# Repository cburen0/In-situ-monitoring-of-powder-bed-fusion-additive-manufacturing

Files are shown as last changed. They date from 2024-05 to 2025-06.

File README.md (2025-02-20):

# In situ monitoring of powder bed fusion additive manufacturing
Hardware and software designs for in situ systems for laser-based powder bed fusion additive manufacturing.

<p align="center">
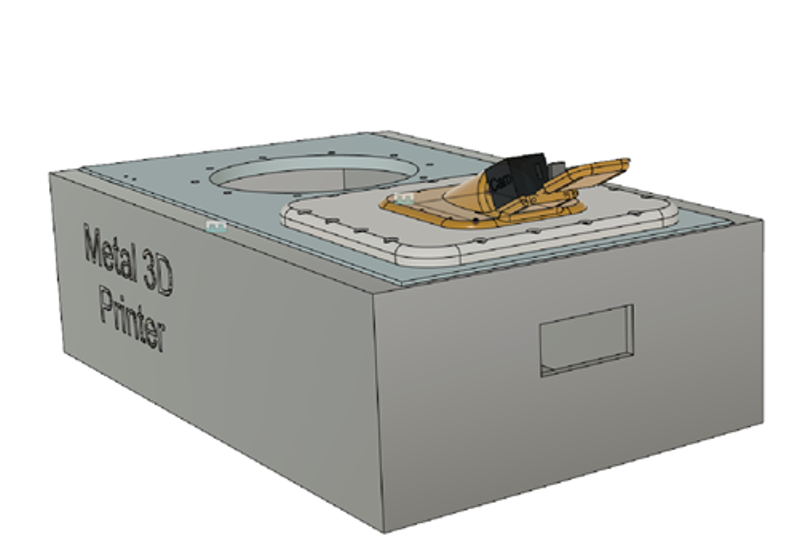
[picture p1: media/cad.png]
 <br> 
The CAD model of in situ systems for laser-based powder bed fusion additive manufacturing. 
</p>

<p align="center">
 <br> 
The Camera setup of in situ systems for laser-based powder bed fusion additive manufacturing.  
</p>

## [System Development](system_development)
The system (hardware and software) design for the project.

## [Aconity MIDI – 3D Reference Models](Aconity_MIDI–3D_Reference_Models)
Simple CAD models for the Aconity MIDI printer used for visualization purposes.

## Licensing and Citation

This work is licensed under a Creative Commons Attribution-ShareAlike 4.0 International License [cc-by-sa 4.0].



#### Bibtex

@Misc{ARTSLabSituMonitoringPowder,  
  author = {{ARTS-L}ab},  
  title  = {In situ monitoring of powder bed fusion additive manufacturing},  
  groups = {{ARTS-L}ab},  
  url    = {https://github.com/ARTS-Laboratory/In-situ-monitoring-of-Powder-bed-fusion-additive-manufacturing},  
}  

<p align="center">
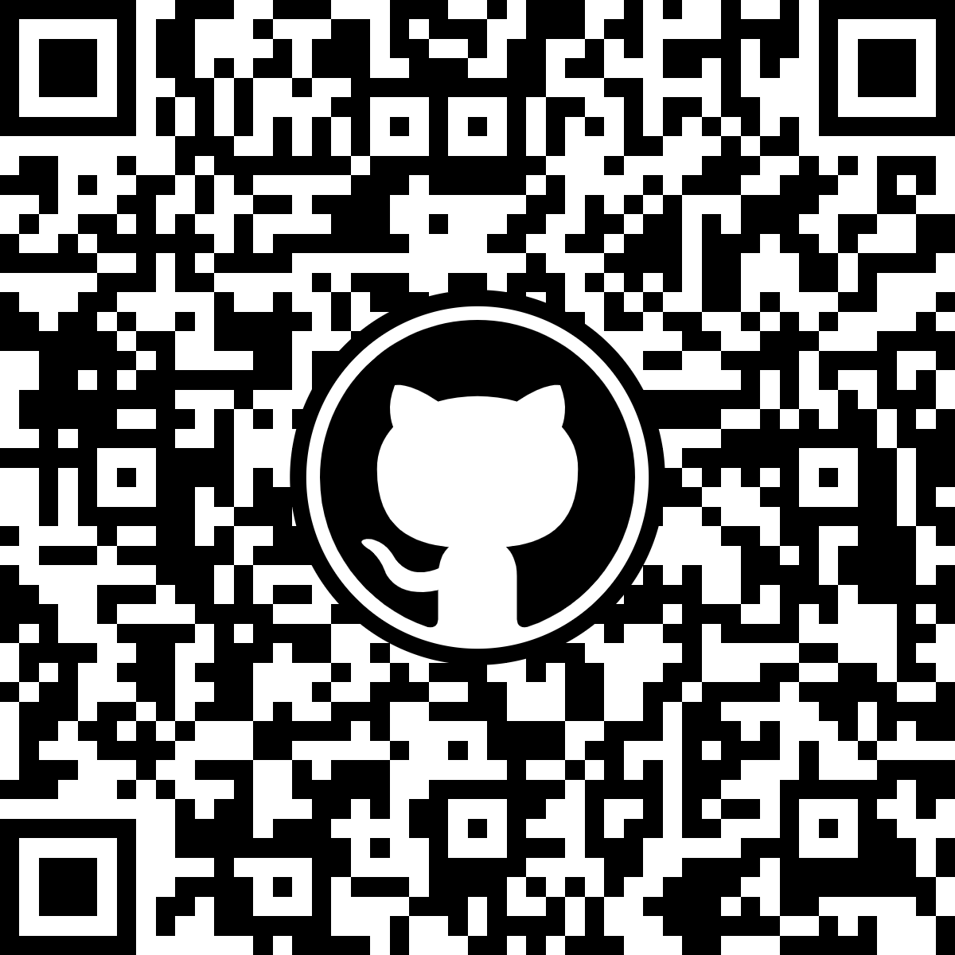
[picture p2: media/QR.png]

</p>
<p align="center">
QR code for repo.
</p>

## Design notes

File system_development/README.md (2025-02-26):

# Systems Variations  
Different system variations (i.e. product lines) are named after mythical materials. 

## Mithril
* A legendary, lightweight, and strong metal from Tolkien’s Middle-earth.
* Sensing system designed with a optical camera.

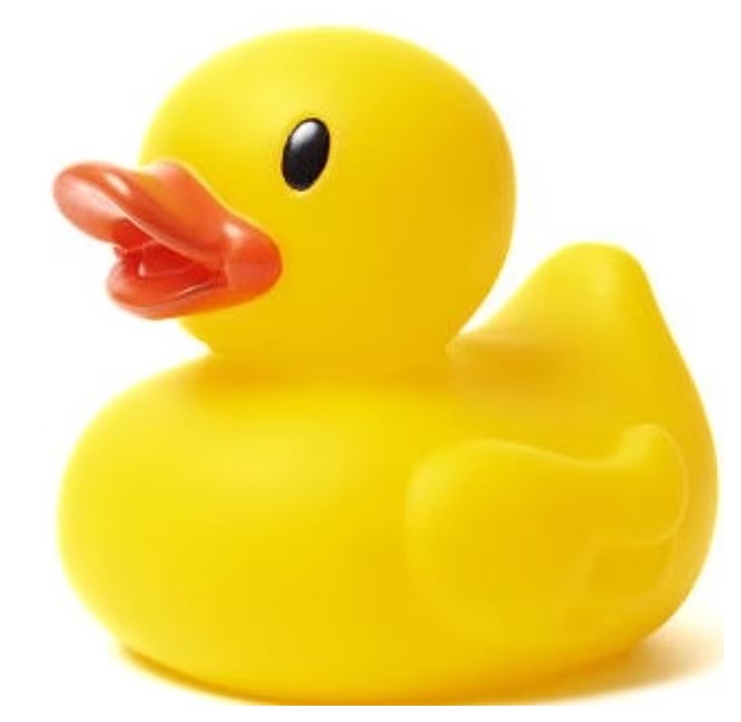
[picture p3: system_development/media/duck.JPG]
 <br> 
The CAD model of in situ systems for laser-based powder bed fusion additive manufacturing. 
</p>

## Adamant
* An ancient term for an unbreakable, diamond-like substance.
* Sensing system designed with a thermal camera.

 <br> 
The CAD model of in situ systems for laser-based powder bed fusion additive manufacturing. 
</p>

## Uru
* A mystical Asgardian metal, known for its magical properties.
* Sensing system designed with an event camera.

 <br> 
The CAD model of in situ systems for laser-based powder bed fusion additive manufacturing. 
</p>

## Orichalcum
* A lost golden-red metal from Atlantis and Greek mythology.
* Sensing system designed with a laser vibrometer.

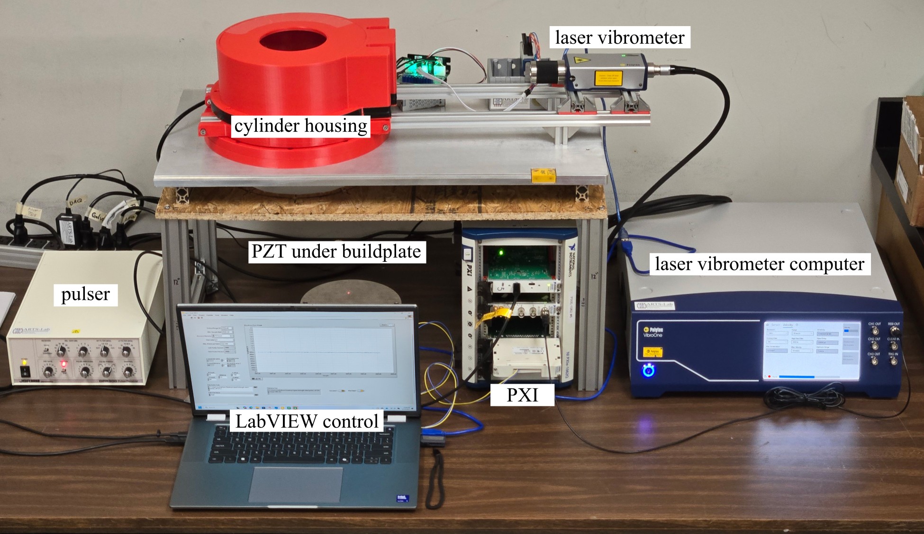
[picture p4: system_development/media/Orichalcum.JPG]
 <br> 
Experimental setup including custom cover assembly, laser vibrometer, piezoelectric transducer, and pulser. 
</p>

## Damascus
* A famed patterned steel, known for strength and sharpness.
* Sensing system designed with multiple sensing systems.

 <br> 
The CAD model of in situ systems for laser-based powder bed fusion additive manufacturing. 
</p>

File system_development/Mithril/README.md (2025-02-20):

# Mithril
Sensing system designed with an optical camera.

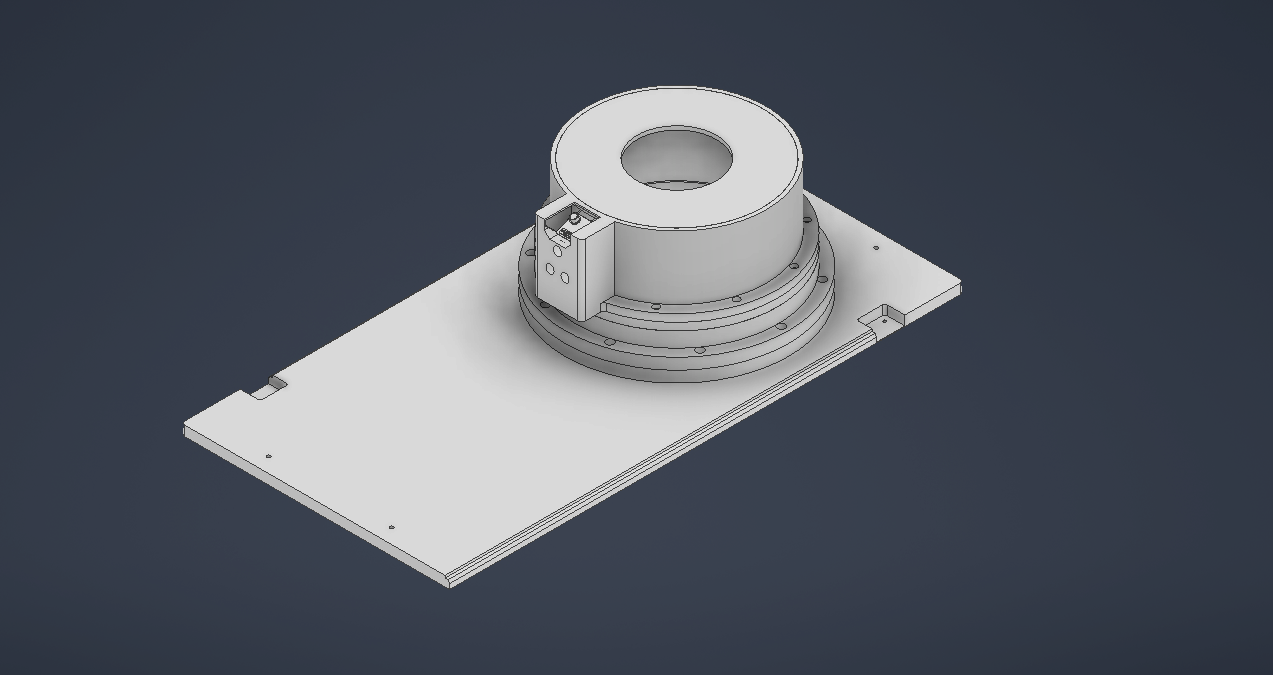
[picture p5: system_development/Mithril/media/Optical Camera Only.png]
 <br> 
The CAD model of in situ systems for laser-based powder bed fusion additive manufacturing. 
</p>

## V0.1
1. Optical camera holder for FLIR.

## V0.2

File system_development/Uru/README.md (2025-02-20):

# Uru
Sensing system designed with an event camera.
## V0.1
1. ...

## V0.2

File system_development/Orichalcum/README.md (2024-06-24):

# Orichalcum
An in situ sensing system with a laser vibrometer.

## V0.1 - Exploriotority 
Initial hardware design for in situ monitoring system.

## V0.2 - System Built as Sub-components
Initial hardware design for in situ monitoring system.

## V0.3 - First Single Prototype
Combining the sub-components of V0.2 into a single hardware design.

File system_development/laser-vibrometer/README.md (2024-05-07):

# Laser Vibrometer

Sensing system designed with a laser vibrometer

## V0.1

## V0.2

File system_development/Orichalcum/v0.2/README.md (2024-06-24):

# V0.2 - System Built as Sub-components
Sensing system designed with a laser vibrometer

## Hardware design
* cover and cylinder pieces which house galvo and laser
 
## Software design
* galvo LabVIEW code

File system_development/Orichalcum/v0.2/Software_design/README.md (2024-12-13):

# Software Design

\data-grid-figure
Preliminary figure generation code in python

\data-processing-code
Python code for generating heat map of surface scan from output data files

\galvo-scanner
LabVIEW for galvo mirror position control through cDAQ

\laser-vibrometer
LabVIEW for collecting Laser Vibrometer Data

\optical-camera
LabVIEW codes for Flir Blackfly optical camera

\v2-cover-control
LabVIEW code for synchronized control of all instruments

\Instrument Manuals
Manufacturer provided material for hardware used

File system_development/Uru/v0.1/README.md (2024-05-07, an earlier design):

# Thermal Camera
Sensing system designed with a thermal camera.

## Hardware design
1. Thermal camera holder for WORKSWELL
 
## Software design

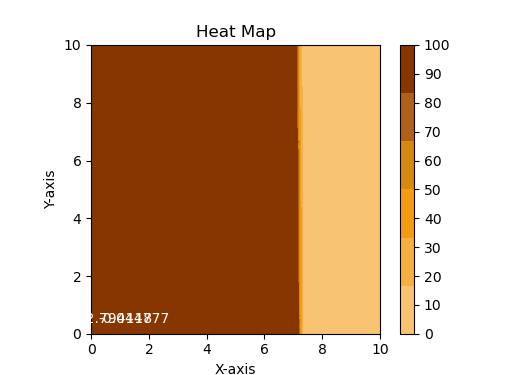
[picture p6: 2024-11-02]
system_development/Orichalcum/v0.2/Software_design/data-grid-figure/Figures/Figure_1.png

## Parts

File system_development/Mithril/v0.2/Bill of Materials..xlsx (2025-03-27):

Name | Quantity | Source
Cover | 1 | Xometry + model
300mm Housing 1 | 1 | 3D Printed
300mm Housing 2 | 1 | 3D Printed
Cylinder Spacer | 1 | 3D Printed
Cylinder Segment Inner | 1 | 3D Printed
Cylinder Segment Outer | 1 | 3D Printed
Cylinder Segment 1 | 1 | 3D Printed
Cylinder Segment Face | 1 | 3D Printed
Camera Bracket | 1 | 3D Printed
Flir Camera Blackfly | 1 | Teledyne Flir Blackfly S USB3 1.6MP Color Camera BFS-U3-16S2C-CS (https://www.bhphotovideo.com/c/product/1844599-REG/teledyne_flir_bfs_u3_16s2c_cs_blackfly_s_usb3_1_6mp.html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)
Welding glass | 1 | Laser Vision (https://lasersafety.com/product/p5p10-window/) | Glass1 (https://www.mscdirect.com/product/details/62674445) | Glass2 (https://www.mscdirect.com/product/details/62674403) | Glass3 (https://www.mscdirect.com/product/details/62674437) | Glass4 (https://www.mscdirect.com/product/details/62674411)
Cover ^ 2 | 1 | 3D Printed
Cover ^ 3 | 1 | 3D Printed
Cylinder Segment Holder | 1 | 3D Printed
Head Thing (metal) | 1 | Xometry + model
M6 x 10 | 4 | M6-1 Thread Size, 10 mm Lg, Socket Head Cap Screw - 26LG36|M07000.060.0010 - Grainger (https://www.grainger.com/product/Socket-Head-Cap-Screw-M6-1-26LG36)
M4 x 14 | 2 | M4-0.7 Thread Size, 14 mm Lg, Socket Head Cap Screw - 4XY51|SC2204014-100P - Grainger (https://www.grainger.com/product/Socket-Head-Cap-Screw-M4-0-4XY51)
M5 x 20 | 10 | https://www.grainger.com/product/Socket-Head-Cap-Screw-M5-0-26LG28
M5 x 50 | 9 | M5-0.8 Thread Size, 50 mm Lg, Socket Head Cap Screw - 6CE82|M07000.050.0050 - Grainger (https://www.grainger.com/product/Socket-Head-Cap-Screw-M5-0-6CE82)
M5 x 16 | 10 | M5-0.8 Thread Size, 16 mm Lg, Socket Head Cap Screw - 23NN83|M51050.050.0016 - Grainger (https://www.grainger.com/product/Socket-Head-Cap-Screw-M5-0-23NN83)
M4 x 12 | 14 | https://www.grainger.com/product/Socket-Head-Cap-Screw-M4-0-22UC39
M3 x 16 | 2 | https://www.grainger.com/product/Socket-Head-Cap-Screw-M3-0-22TZ13
M3 x 8 | 3 | https://www.grainger.com/product/Socket-Head-Cap-Screw-M3-0-22TY48
M3 x 35 | 2 | https://www.grainger.com/product/Socket-Head-Cap-Screw-M3-0-22UC31
M3 x 25 | 1 | https://www.grainger.com/product/Socket-Head-Cap-Screw-M3-0-22UC28
M5 nut | 21 | https://www.grainger.com/product/Hex-Nut-M5-0-80-Thread-22YK31
M3 nut | 3 | https://www.grainger.com/product/Hex-Nut-M3-0-50-Thread-6CA29
M4 nut | 2 | https://www.grainger.com/product/Hex-Nut-M4-0-70-Thread-22UK82
Pull Handle | 2 | https://www.grainger.com/product/JW-WINCO-Pull-Handle-Unthreaded-Holes-813RC8

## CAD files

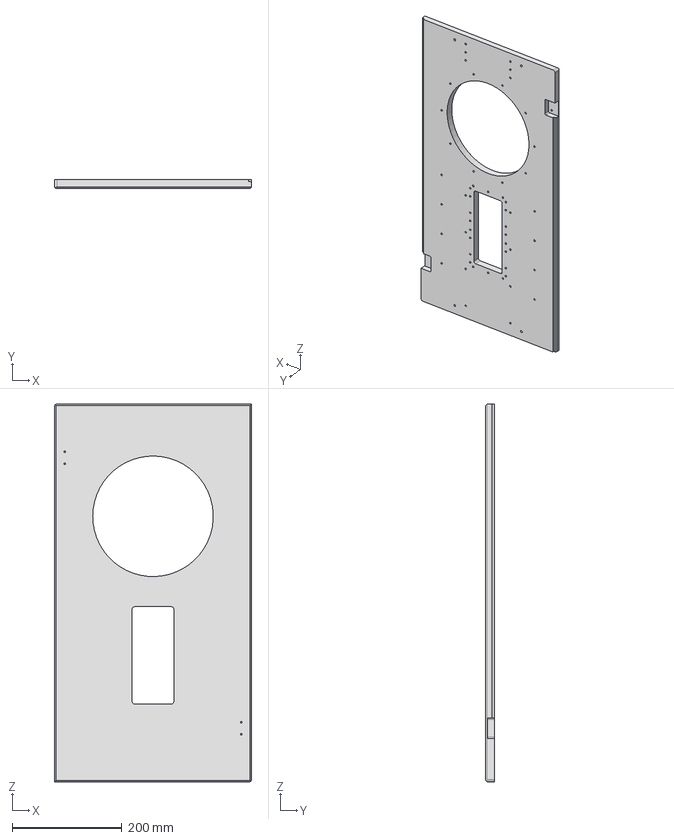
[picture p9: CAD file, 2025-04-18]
system_development/Orichalcum/v0.2/Hardware_design/custom-cover/cover/Updated Cover (Vibrometer).stp
360.0 x 15.9 x 690.0 mm

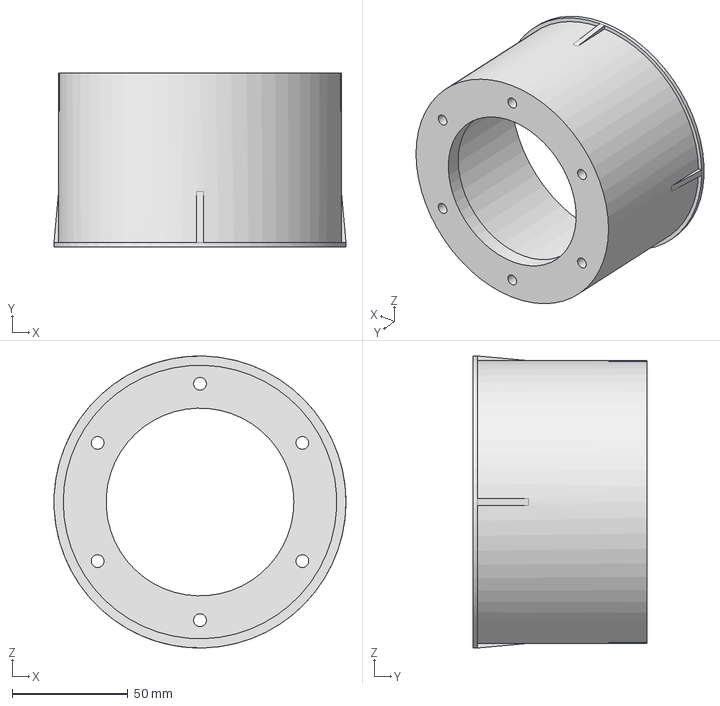
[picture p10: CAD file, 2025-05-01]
system_development/Orichalcum/v0.2/Hardware_design/custom-cover/cylinder-parts/cylinder-segments/Replacement Rings/C .Replace - Face v0.2.stp
126.0 x 75.0 x 126.0 mm

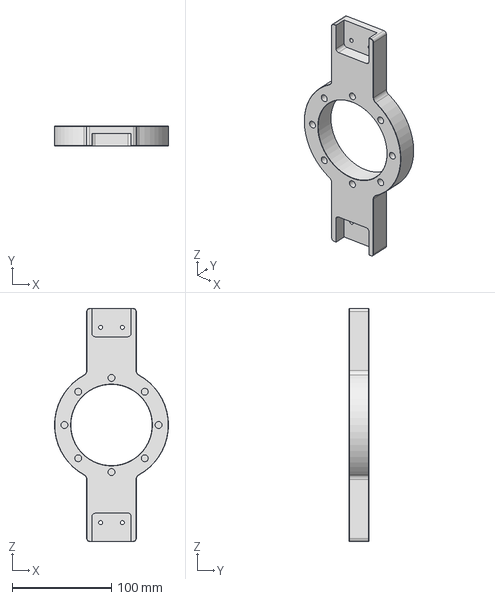
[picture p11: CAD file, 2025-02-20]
system_development/Orichalcum/v0.2/Hardware_design/custom-cover/cylinder-parts/stl-files-full pieces/Head Thing.stp
115.0 x 20.0 x 235.0 mm

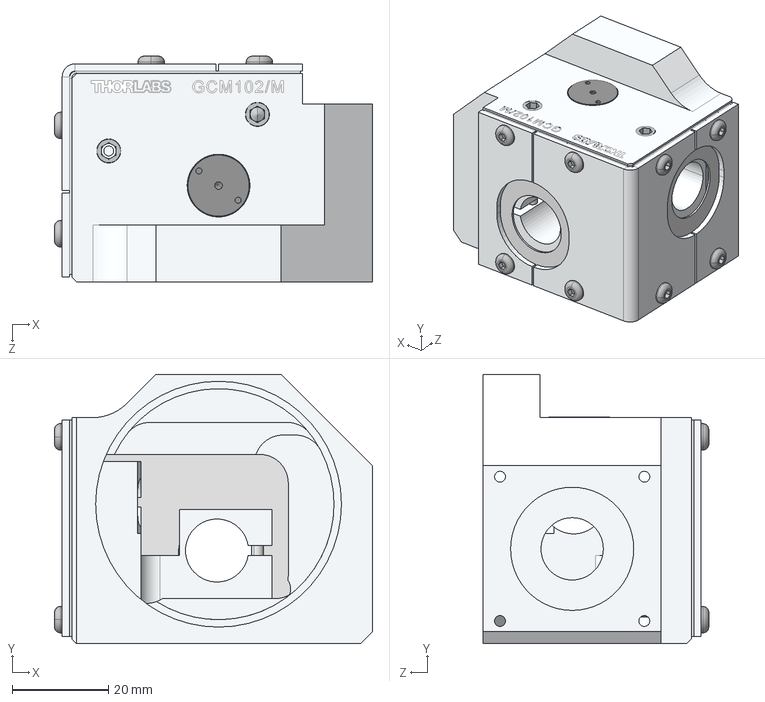
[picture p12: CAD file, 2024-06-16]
system_development/Orichalcum/v0.2/Hardware_design/galvo-scanner/GCM102_M-Step.step
66.1 x 56.0 x 46.9 mm

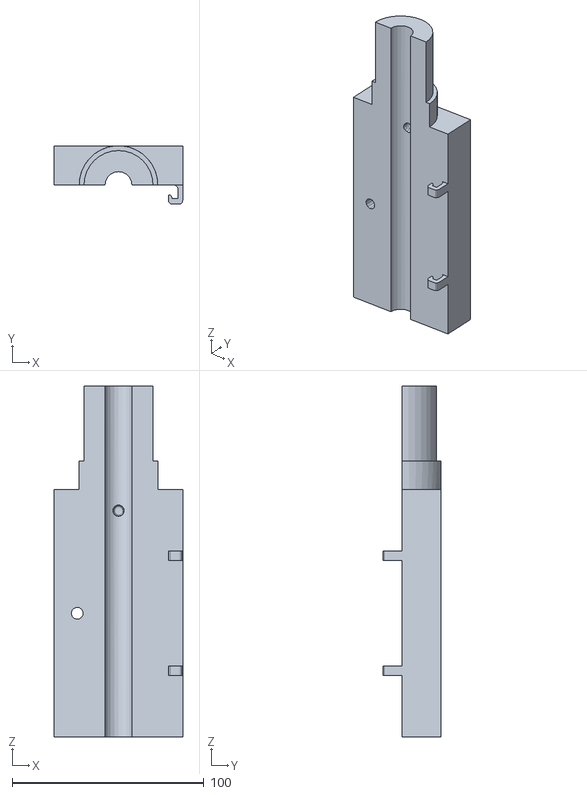
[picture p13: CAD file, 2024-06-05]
system_development/Orichalcum/v0.2/Hardware_design/laser-vibrometer/stl-files/Pen_Housing_Top_V2.stl
67.0 x 30.5 x 183.0

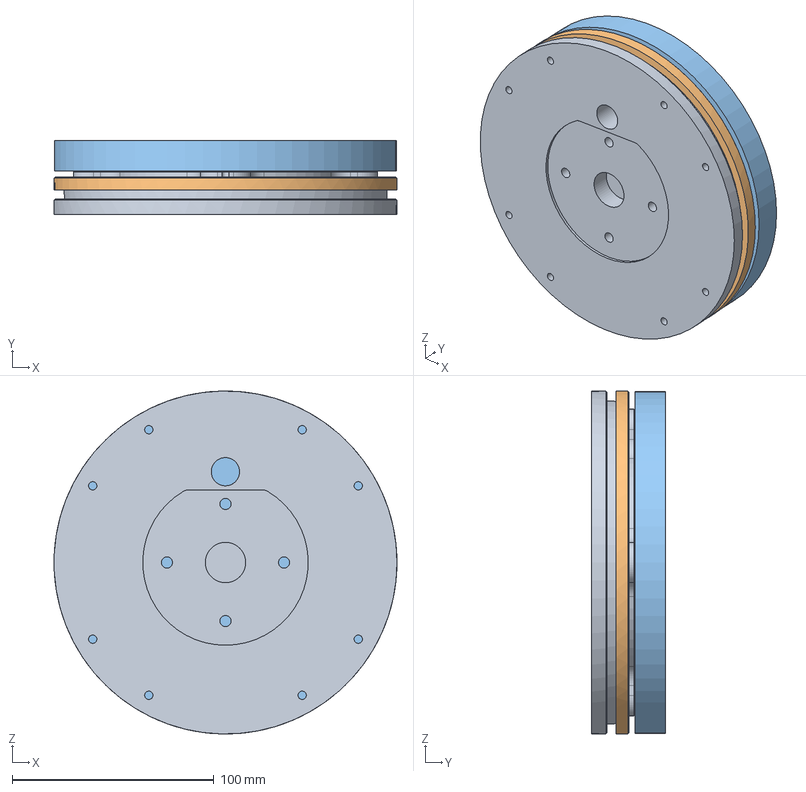
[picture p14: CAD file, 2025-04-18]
system_development/Orichalcum/v0.2/Hardware_design/pzt-parts/Assemblies/Built Platform (metal) + Clamp Ring.stp
170.0 x 36.5 x 170.0 mm
Build Plateform one Indents
Clamp Ring
substrate plate

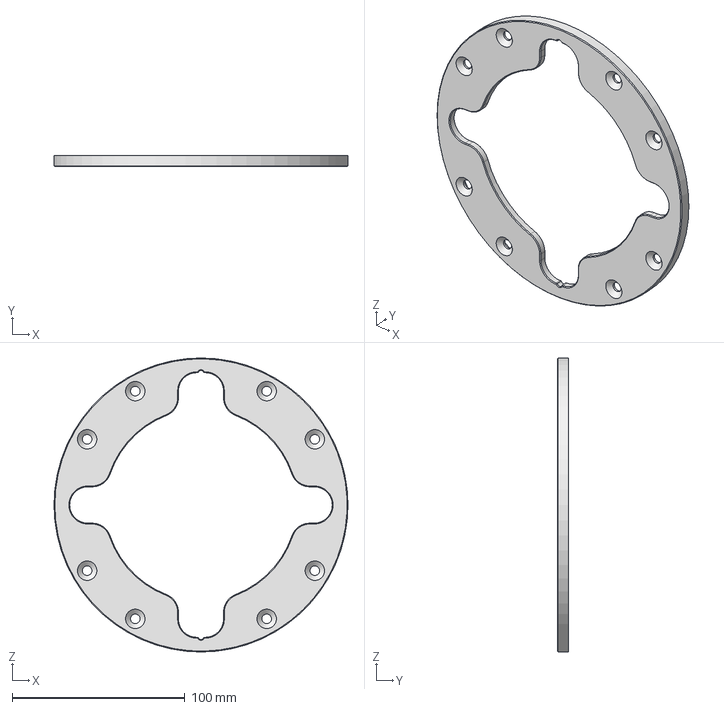
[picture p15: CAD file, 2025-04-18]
system_development/Orichalcum/v0.2/Hardware_design/pzt-parts/Build Platform/Clamp Ring.stp
170.0 x 6.50 x 170.0 mm

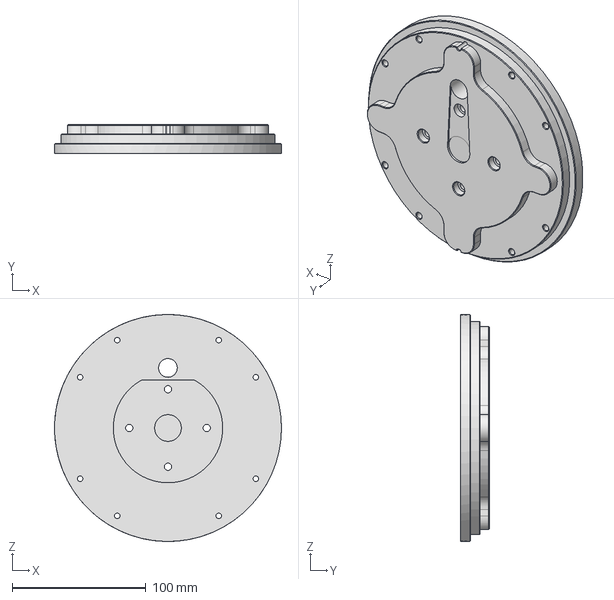
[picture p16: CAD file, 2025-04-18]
system_development/Orichalcum/v0.2/Hardware_design/pzt-parts/Build Platform/Metal/Build Plateform one Indents (metal).stp
170.0 x 21.5 x 170.0 mm

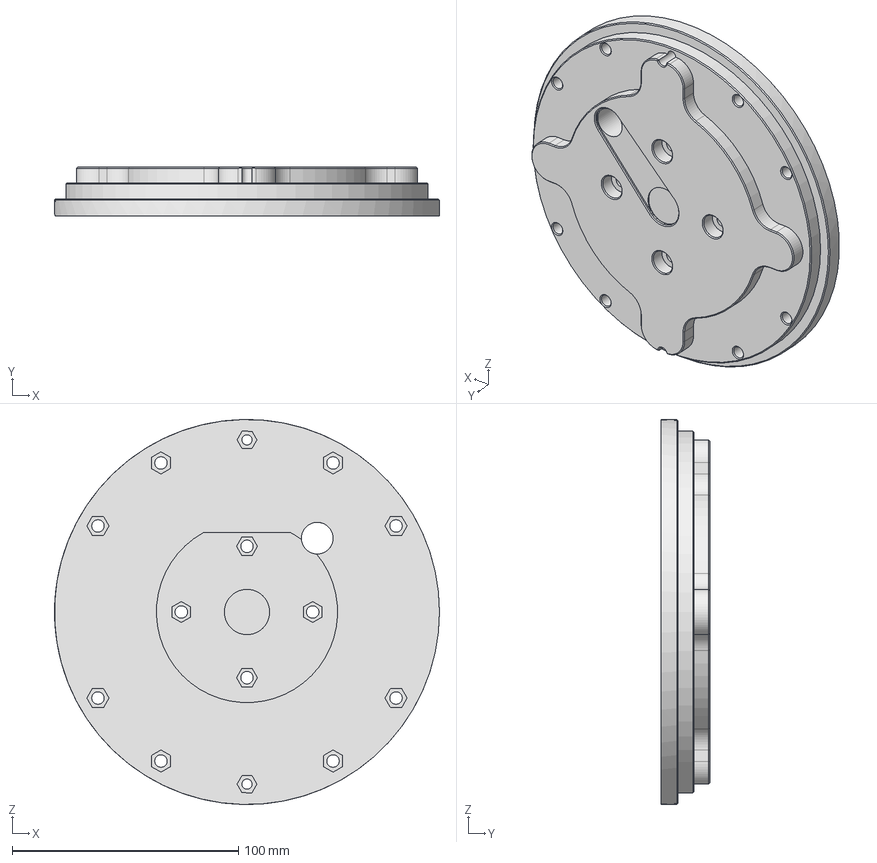
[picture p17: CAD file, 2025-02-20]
system_development/Orichalcum/v0.2/Hardware_design/pzt-parts/STIL file/Build Plateform one Indents (plastic) 3.stp
170.0 x 21.5 x 170.0 mm

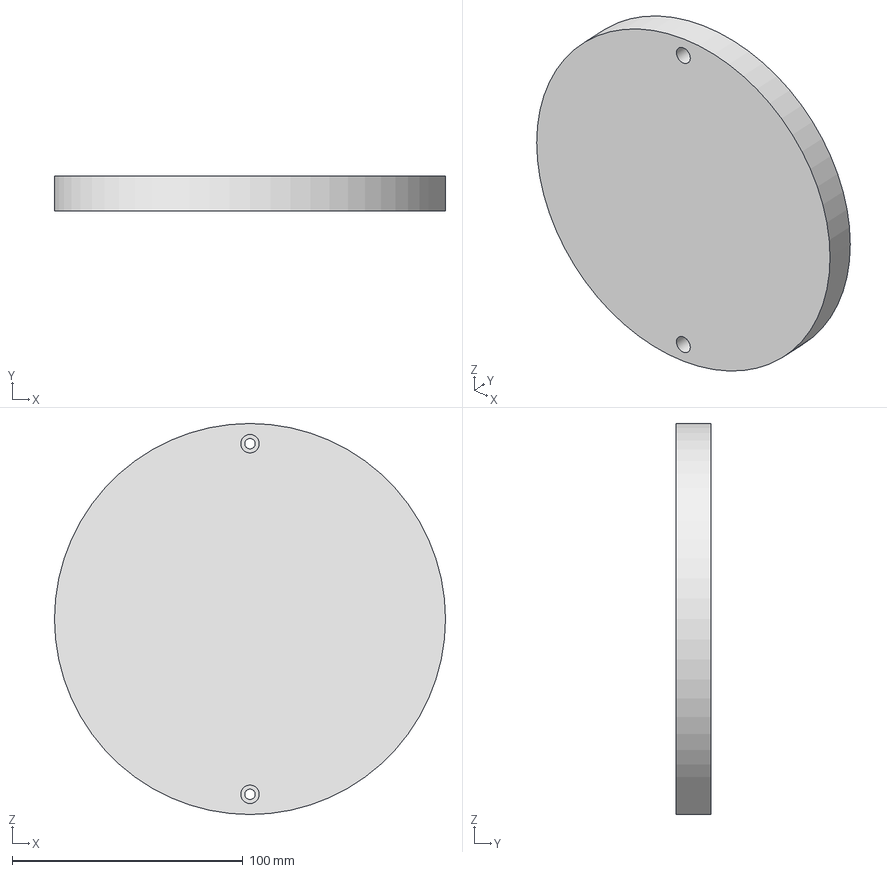
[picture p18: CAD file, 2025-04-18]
system_development/Orichalcum/v0.2/Hardware_design/pzt-parts/Substrate plates/substrate plate.stp
169.5 x 15.0 x 169.5 mm

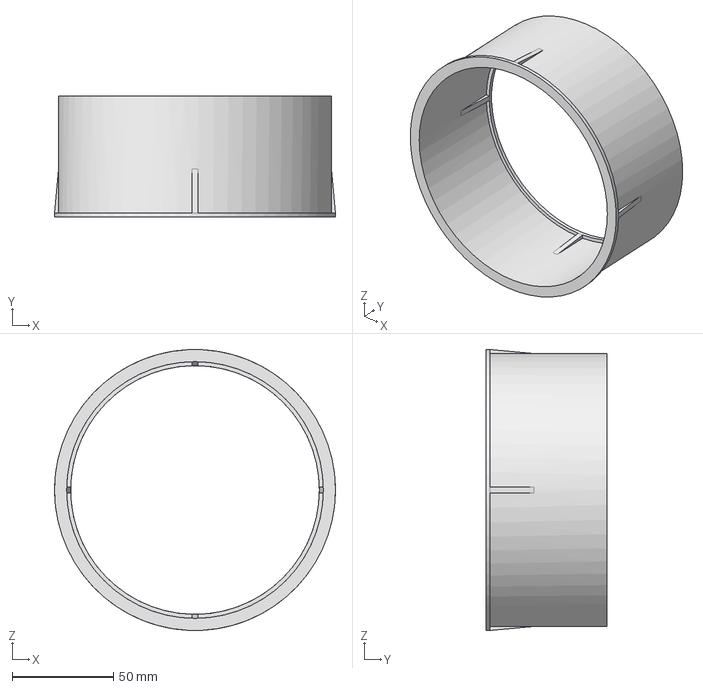
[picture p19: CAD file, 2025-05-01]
system_development/Orichalcum/v0.2/Hardware_design/custom-cover/cylinder-parts/cylinder-segments/Replacement Rings/C .Replace - 10 v0.2.stp
139.0 x 60.0 x 139.0 mm

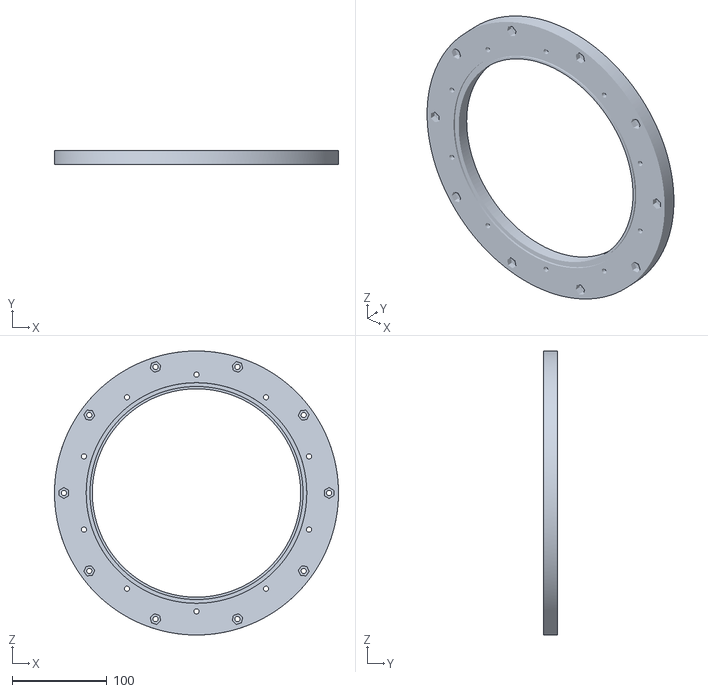
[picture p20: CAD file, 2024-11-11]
system_development/Orichalcum/v0.2/Hardware_design/custom-cover/cylinder-parts/stl-files-full pieces/260mm Housing 1.stl
300.0 x 15.0 x 300.0

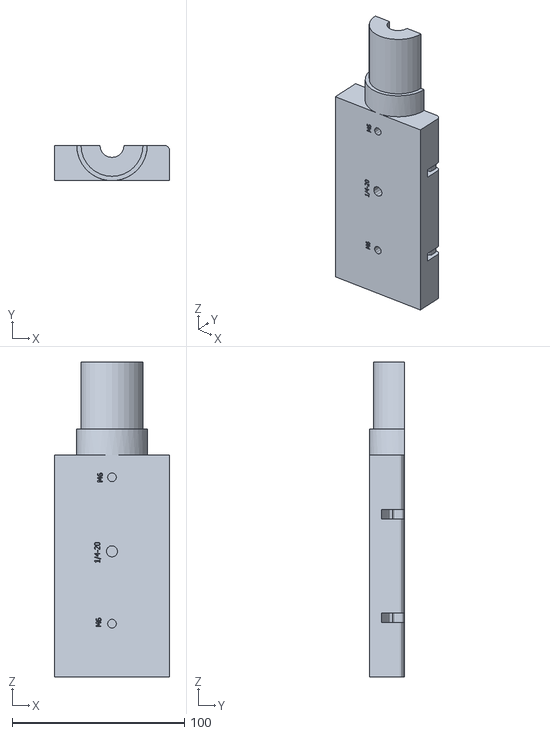
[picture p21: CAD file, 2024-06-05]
system_development/Orichalcum/v0.2/Hardware_design/laser-vibrometer/stl-files/Pen_Housing_Bottom_V2.stl
67.0 x 20.5 x 183.0

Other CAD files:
system_development/Orichalcum/v0.2/Hardware_design/pzt-parts/Drawings/Build Plateform one Indents.dwg
system_development/Uru/v0.3/CAD/ASM/Drawings/Head Thing (metal).dwg
system_development/Uru/v0.3/CAD/ASM/Step/Printer Settings ender 5 plus 0.6mm.3mf
system_development/Orichalcum/v0.2/Hardware_design/custom-cover/cover/Updated Cover (Vibrometer) 1.stp
system_development/Orichalcum/v0.2/Hardware_design/pzt-parts/STIL file/Build Plateform one Indents (metal).stp
system_development/Mithril/v0.1/hardware design/flir_holder.f3d
system_development/Mithril/v0.1/hardware design/flir_holder.ipt
system_development/Mithril/v0.1/hardware design/flir_holder.stl
system_development/Mithril/v0.2/Model/Cover Optical Camera Only.iam
system_development/Mithril/v0.2/Model/Cylinder Segment/Cylinder Segment Camera Only/OldVersions/C .Replace - 10.0006.ipt
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

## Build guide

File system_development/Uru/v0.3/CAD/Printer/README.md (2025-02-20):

# Aconity MIDI – 3D Reference Models
Assembly of the printer we are working with.

<p align="center">
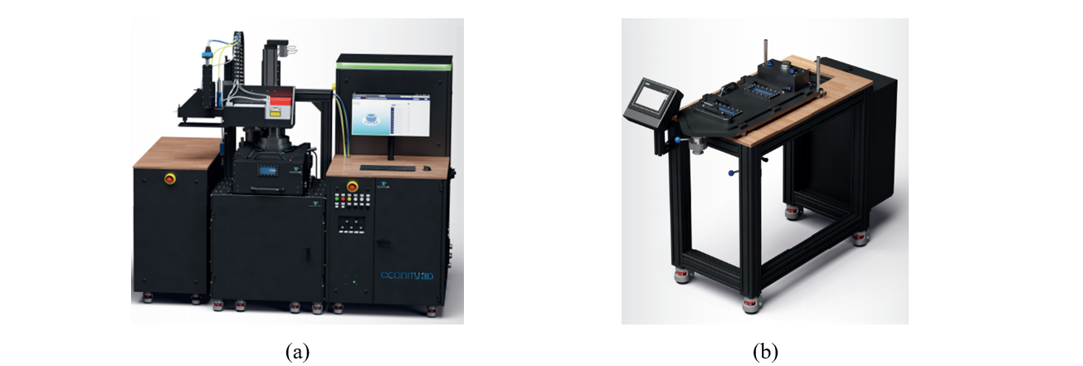
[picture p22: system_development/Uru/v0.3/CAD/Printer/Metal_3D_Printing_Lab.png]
Figure Caption
  
</p>

**Figure 1:** Aconity MIDI Metal 3d printer, showing the: (a) Aconity MIDI, metal LPBFAM printer, and; (b)
sieve station for powder recycling.

## Cover
* The cover or lid for the printer (no cylinder)

## Laser w/ Silver
* Laser platform assembly

## Inner chamber piece
* Piece that adds new powder over the previous layer

## Overhead Laser Unit
* Laser unit, a part of Laser w/ Silver assembly

## Silver 
* Rail that the laser unit rides on

## Cylinders
* Contains the telescoping rings that mate with the laser assembly

## Printer Assembly
* Full printer assembly with all parts

## Printer Body 
* Printer chamber

## Printer Cover
* Cover assembly with Cylinder

## Printer Frame 
* Many parts are attached to the frame

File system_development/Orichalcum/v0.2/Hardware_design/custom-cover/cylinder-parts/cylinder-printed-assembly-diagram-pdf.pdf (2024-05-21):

# Cylinder Assembly Chopped

## The following is designed… - to be used with M8 Socket Head Bolts of ~3cm length and M8 Lock Nuts - and to be printed on a 235x235mm 3D printer bed

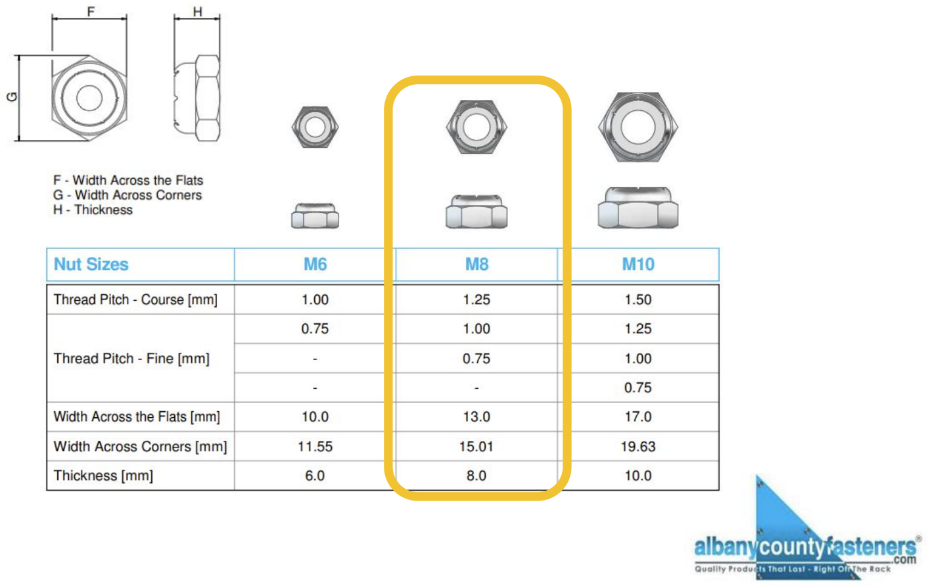
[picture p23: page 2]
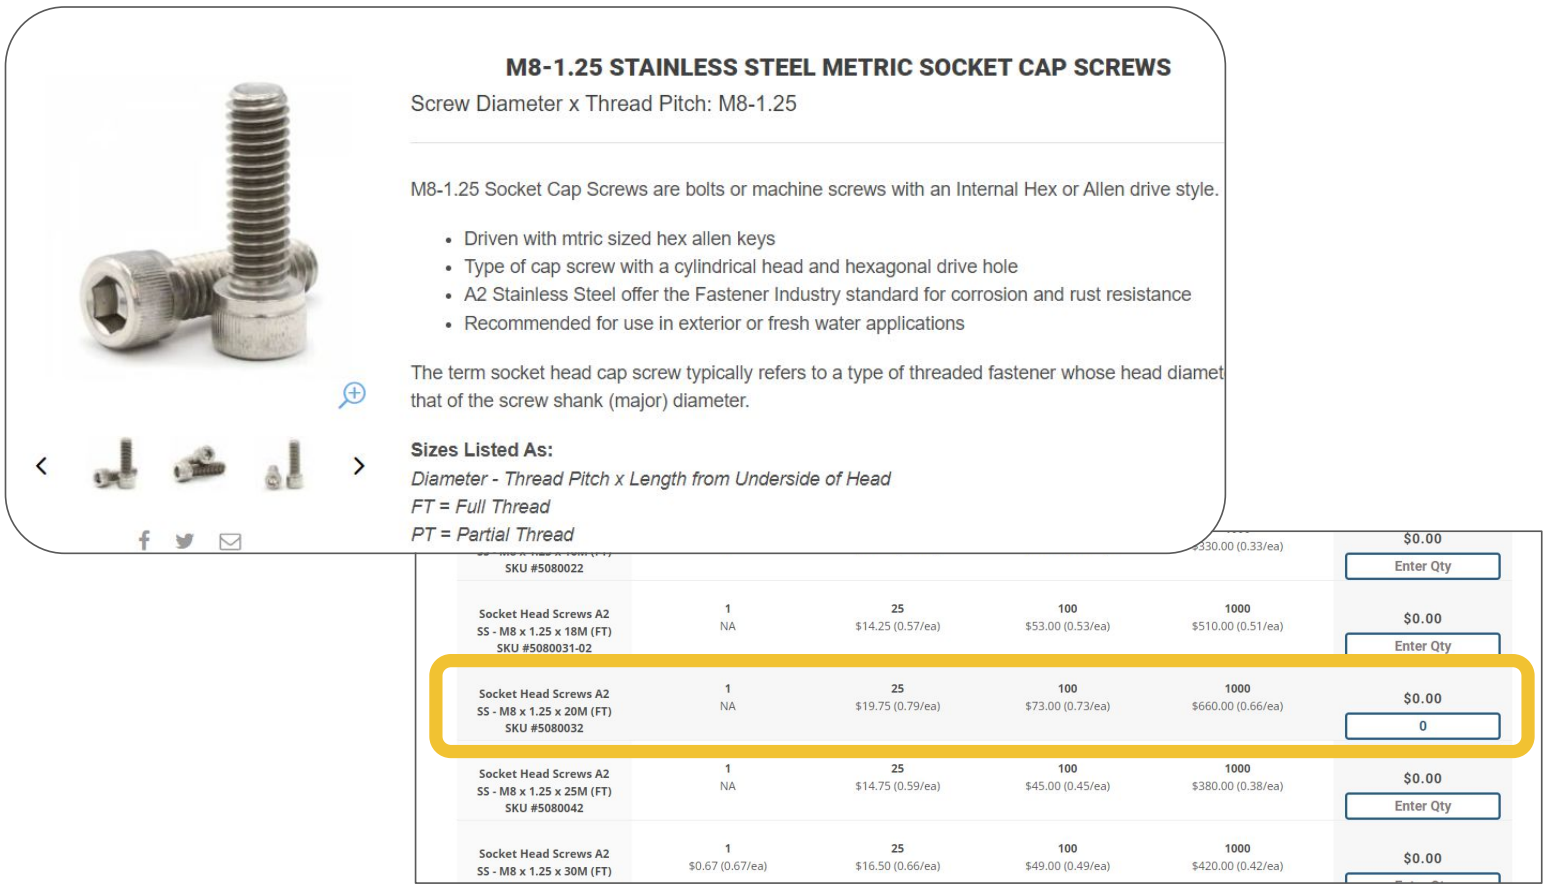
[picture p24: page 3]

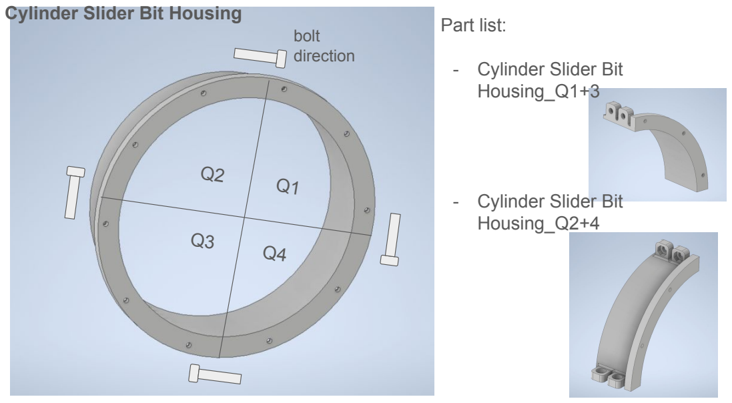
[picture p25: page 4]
Part list:; bolt direction

Cylinder Slider Bit Housing

- Cylinder Slider Bit
Housing_Q1+3

Housing_Q2+4

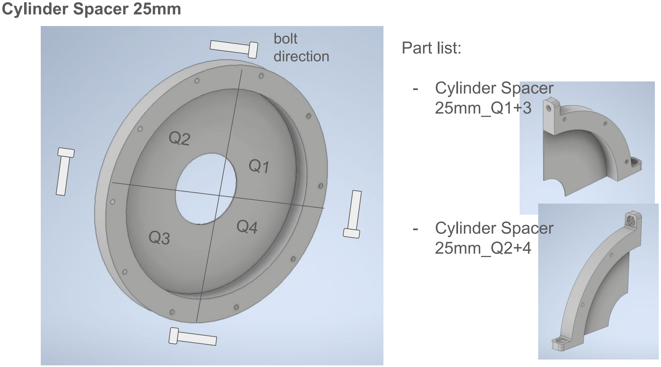
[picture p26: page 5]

Q1

Q2

Q3

Q4

Part list:

- Cylinder Spacer
25mm_Q1+3
- Cylinder Spacer
25mm_Q2+4

bolt
direction

Cylinder Spacer 25mm

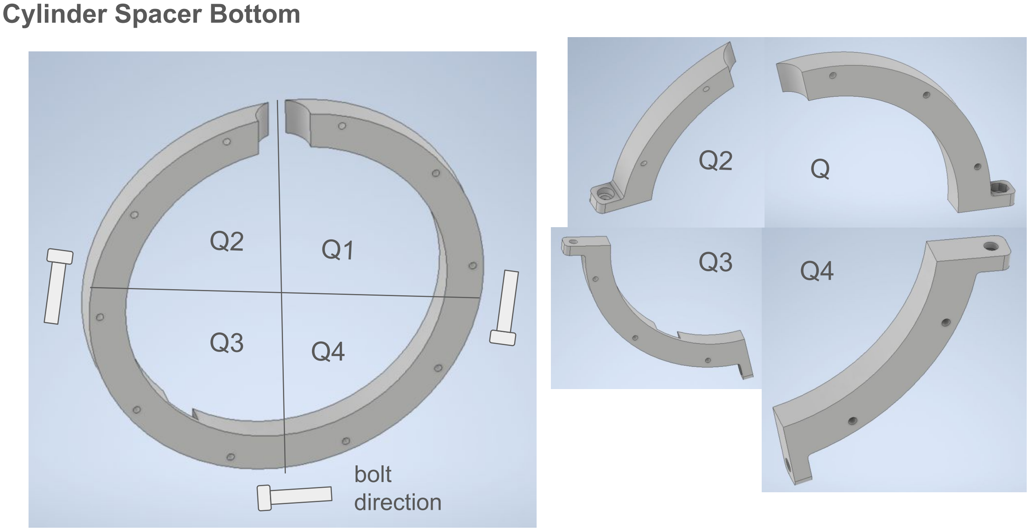
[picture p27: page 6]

Q2 Q1

Q3 Q4

bolt
direction

Q2 Q

Q3 Q4

Cylinder Spacer Bottom

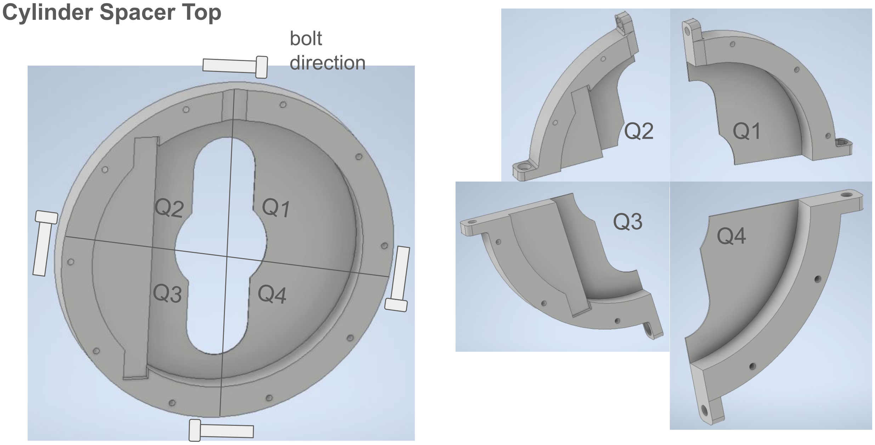
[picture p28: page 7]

Q2

Q1

Q3
Q4

bolt
direction
Q2 | Q1

Q3 Q4

Cylinder Spacer Top

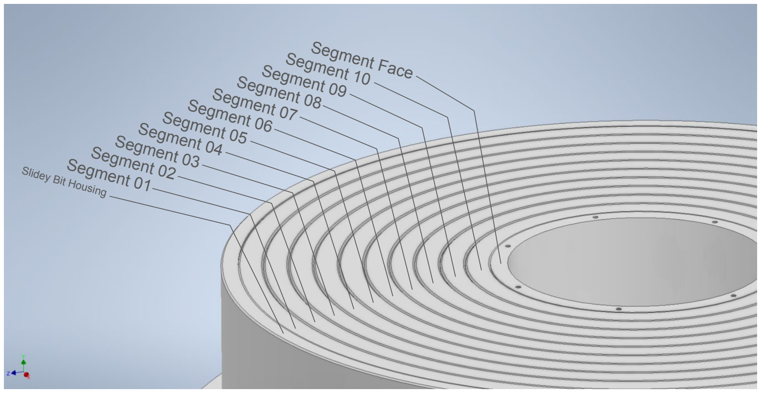
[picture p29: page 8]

Segment Face
Segment 10

Segment 07
Segment 06
Segment 05
Segment 04
Segment 03
Segment 02
Segment 01

Segment 09
Segment 08

Slidey Bit Housing

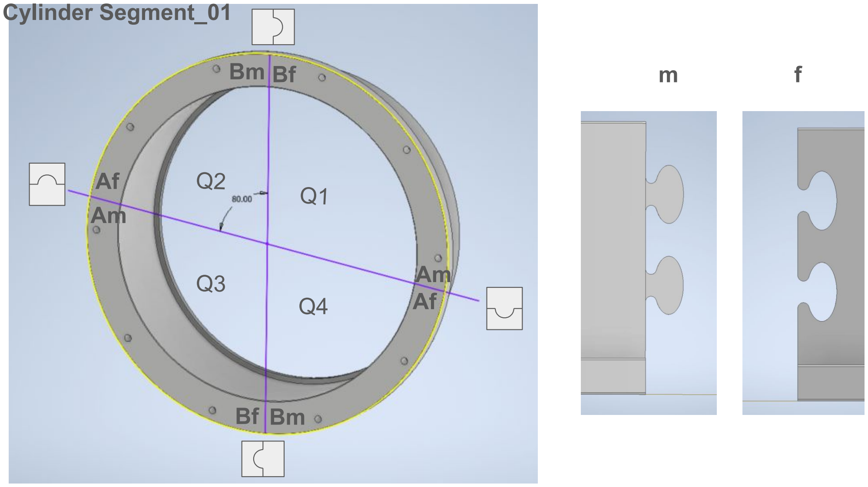
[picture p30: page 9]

Cylinder Segment_01

Q1 Q2

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
Bf Bm

m | f

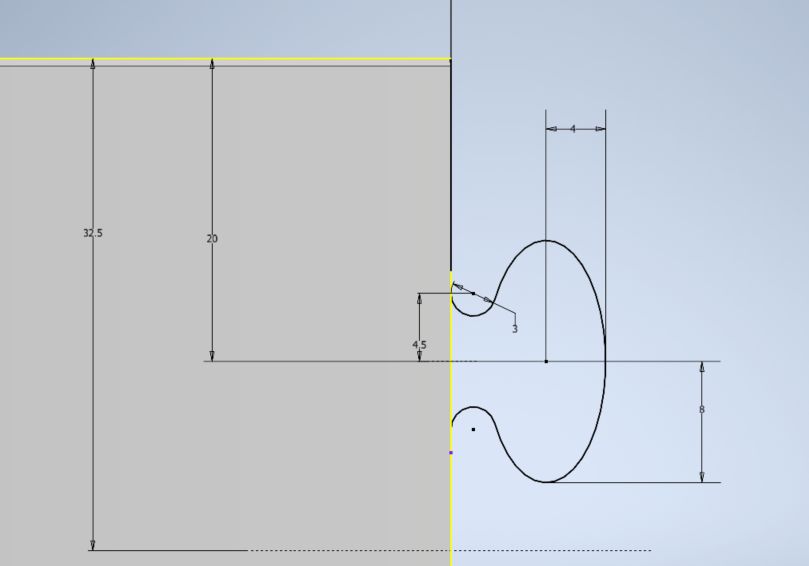
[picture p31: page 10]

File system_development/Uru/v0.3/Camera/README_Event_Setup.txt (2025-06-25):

Installation Guide. Since the files to be able to control the event camera are over 5ish GB I can't to upload them to the GitHub. 
I followed the guide so you can ignore this file and just look at the website, but I added more onto it so it should help with simplicity. If you have any questions you can contact me at cburen@email.sc.edu 

Note: CMD/PS will be interchangeably it doesn't matter which one you use. If you are using CMD then remove the .\ from the beginning of the input, and if you're using powershell you might have to add it

1. Follow the guide: https://docs.prophesee.ai/stable/installation/windows_openeb.html#chapter-installation-windows-openeb
	1.1 Install Metavision from https://docs.prophesee.ai/stable/installation/index.html
	1.2 Install git
	1.3 Install CMake 3.26 (more recent versions might not be compatible)
	1.4 Install Microsoft Visual C++ compiler (MSVC, 64-bit version) included in Visual Studio 2022 - Fall 2023 LTSC (version 17.8). 	    If you install the Build Tools only, make sure Windows 10 SDK is checked, and add English Language Pack.
	1.5 Enable long paths by 
		1. Hit the Windows key, type gpedit.msc and press Enter
		2. Navigate to Local Computer Policy > Computer Configuration > Administrative Templates > System > Filesystem
		3. Double-click the “Enable Win32 long paths” option, select the “Enabled” option and click “OK”
	1.6 Install ffmpeg and add the directory to you paths. 

2. Clone the repos:
	a) openb: https://github.com/prophesee-ai/openeb
		-The install location will be referred to <openb>
			-Ex: C:\Users\CBUREN\Documents\GitHub\vcpkg
	b) https://github.com/microsoft/vcpkg
		-The install location will be referred to <vcpkg>
			-Ex: C:\Users\CBUREN\Documents\GitHub\openeb

3. Using powershell do the following
	3.1 cd <vcpkg>
	3.2 .\bootstrap-vcpkg.bat
	    .\vcpkg update
	3.3 git pull
	3.4 .\vcpkg install boost-thread:x64-windows

4. Then go to C:\<openb>\utils\windows and copy the vcpkg-openeb.json into <vcpkg> and change the name to vcpkg.json
	4.1 Open the file and copy the COPYTHIS.txt into it

5. Then using PowerShell again in the cd vcpkg enter ".\vcpkg install --triplet x64-windows"

6. If failed then do the following
	6.1 .\vcpkg remove boost-thread --recurse
	6.2 .\vcpkg remove boost --recurse
	6.3 Remove-Item -Recurse -Force .\buildtrees
	6.4 Remove-Item -Recurse -Force .\packages
	6.5 Remove-Item -Recurse -Force .\installed
	6.6 Then use update and git pull
	6.7 If these steps didn't work then find error that what was listed and go to the error logs 
		-The error logs can be found in <vcpkg>\buildtrees. Then go to the file that corresponds to the error. 

7. Download and setup Python
	7.1 Must be 3.12
		7.1.1 Added the directories to you paths. 
	7.2 Virtual Environment
		7.2.1 Launch Visual Studio and open the terminal
		7.2.2 In the terminal enter: python -m venv C:\tmp\prophesee\py3venv --system-site-package
		7.2.3 Enter in terminal: pip install "pybind11[global]"
		7.2.4 Enter in terminal: set PYTHONNOUSERSITE=true
		7.2.5 Enter in terminal: C:\tmp\prophesee\py3venv\Scripts\python -m pip install pip --upgrade
C:\tmp\prophesee\py3venv\Scripts\python -m pip install -r <openeb>\utils\python\requirements_openeb.txt
			
8. Compilation using Visual Studio 
Note if you want you can use CMake for the compilation, but I didn't test this
	8.1 Open CMD and enter:
		8.1.1 cd <openeb>
		8.1.2 mkdir build
		8.1.3 cd build
		8.1.4 cmake .. -G "Visual Studio 17 2022" -A x64 -DCMAKE_BUILD_TYPE=Release -DCMAKE_TOOLCHAIN_FILE=C:<openeb>\cmake\toolchains\vcpkg.cmake -DVCPKG_DIRECTORY=<vcpkg> -DBUILD_TESTING=OFF 

			Note: -DCMAKE_TOOLCHAIN_FILE needs to be an absolute path
			      -If you get the error "CMake Error at cmake/custom_functions/python3.cmake:178 (find_package):
  	    		       By not providing "Findpybind11.cmake" in CMAKE_MODULE_PATH this project has
  	 		       asked CMake to find a package configuration file provided by "pybind11",
  	    		       but CMake did not find one."  
				!!!!!-Then you should cd <vcpkg> then enter: .\vcpkg install pybind11:x64-windows
			      -If you get the error "CMake Error at C:/Program Files/Prophesee/third_party/share/hdf5/hdf5-config.cmake:25 			       (message):
  	    		       File or directory C:/Program Files/Prophesee/third_party/tools/hdf5
  	    		       referenced by variable HDF5_TOOLS_DIR does not exist !"
				!!!!! Then cd <vcpkg> and enter: .\vcpkg install hdf5:x64-windows

	8.2 Open metavision.sln in Visual Studio
		8.2.1 Mine was located at: C:\Users\CBUREN\Documents\GitHub\openeb\build
		8.2.2 At the top near the green play button at the top select release from the drop down menu and hit the play button. 
		8.2.3 Go to Solution Explorer right click ALL_BUILD and hit build and then do the same for INSTALL
	8.3 You can either do option 1 or 2. I did option 2 so I suggest that you do that
		8.3.1 Append C:\Program Files\Prophesee\bin to PATH
		8.3.2 append C:\Program Files\Prophesee\lib\metavision\hal\plugins to MV_HAL_PLUGIN_PATH
		8.3.3 append C:\Program Files\Prophesee\lib\hdf5\plugin to HDF5_PLUGIN_PATH

9. Camera Plugins
	9.1 Download wdi-simple.exe from https://kdrive.infomaniak.com/app/share/975517/cb164518-e68f-49fd-a6a1-eea693783bd2/preview/unknown/90270

	9.2 As an administer launch CMD then enter: "wdi-simple.exe -n "EVK" -m "Prophesee" -v 0x04b4 -p 0x00f4
wdi-simple.exe -n "EVK" -m "Prophesee" -v 0x04b4 -p 0x00f5
wdi-simple.exe -n "EVK" -m "Prophesee" -v 0x04b4 -p 0x00f3"

10. Run Tests
	10.1 Download OpenEB test data (it is 1.5gb)
	10.2 If needed make a new folder in <openeb> called datasets
		10.2.1 In datasets make a new folder called openeb. You'll place the raw files in this folder.
	10.3 cd <openeb>/build
	10.4 cmake .. -A x64 -DCMAKE_TOOLCHAIN_FILE=<openeb>\cmake\toolchains\vcpkg.cmake -DVCPKG_DIRECTORY=<vcpkg> -DBUILD_TESTING=ON 
		Note: I would make both paths absolute paths
		10.4.1 If you get the error about pytest then you need to open a new PS and enter 
			C:\tmp\prophesee\py3venv\Scripts\activate
			python -m pip install pytest

		10.4.2 If you get error about gtest remove vcpkg.json from <vcpkg> and then cd <vcpkg> and enter .\vcpkg install gtest --triplet x64-windows
	
	10.5 Then compile by entering into PS: cmake --build . --config Release --parallel 4
	10.6 After you do that you can now use EVT_PS
		10.6.1 Can work with any .exe in <openeb>\bin\Release, but is designed for the evt ones. 

11. Getting the raw files
	11.1 cd into the folder that you want to put the .csv into
	11.2 Use Event_PS to get the powershell code and then copy the code into PS

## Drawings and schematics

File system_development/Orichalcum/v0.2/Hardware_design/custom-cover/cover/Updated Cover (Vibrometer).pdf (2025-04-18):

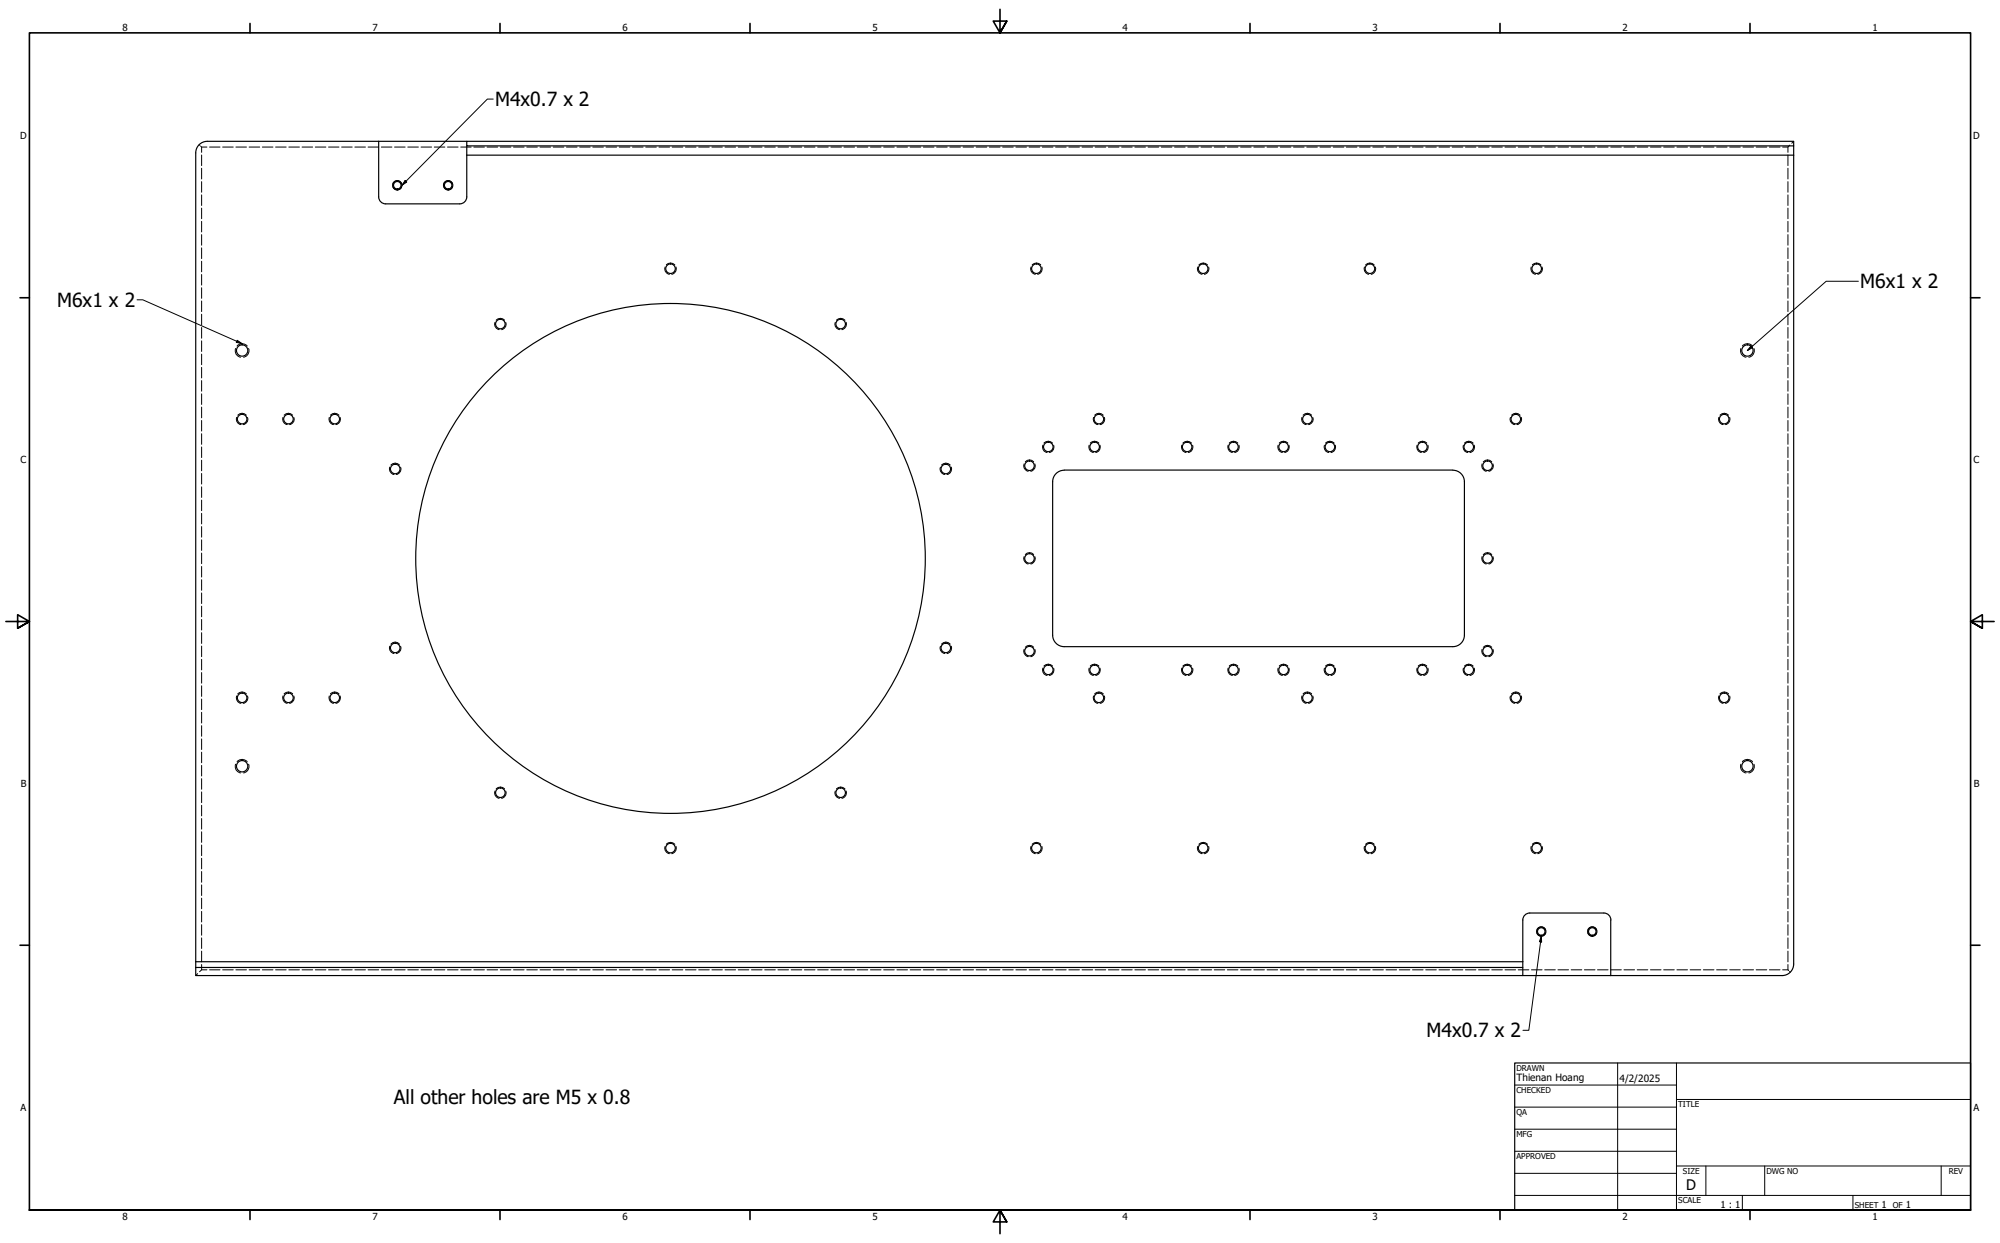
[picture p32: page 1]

DRAWN Thienan Hoang | 4/2/2025

CHECKED

All other holes are M5 x 0.8

MFG

APPROVED

SIZE D | DWG NO | REV

SCALE 1 : 1 | | SHEET 1 OF 1

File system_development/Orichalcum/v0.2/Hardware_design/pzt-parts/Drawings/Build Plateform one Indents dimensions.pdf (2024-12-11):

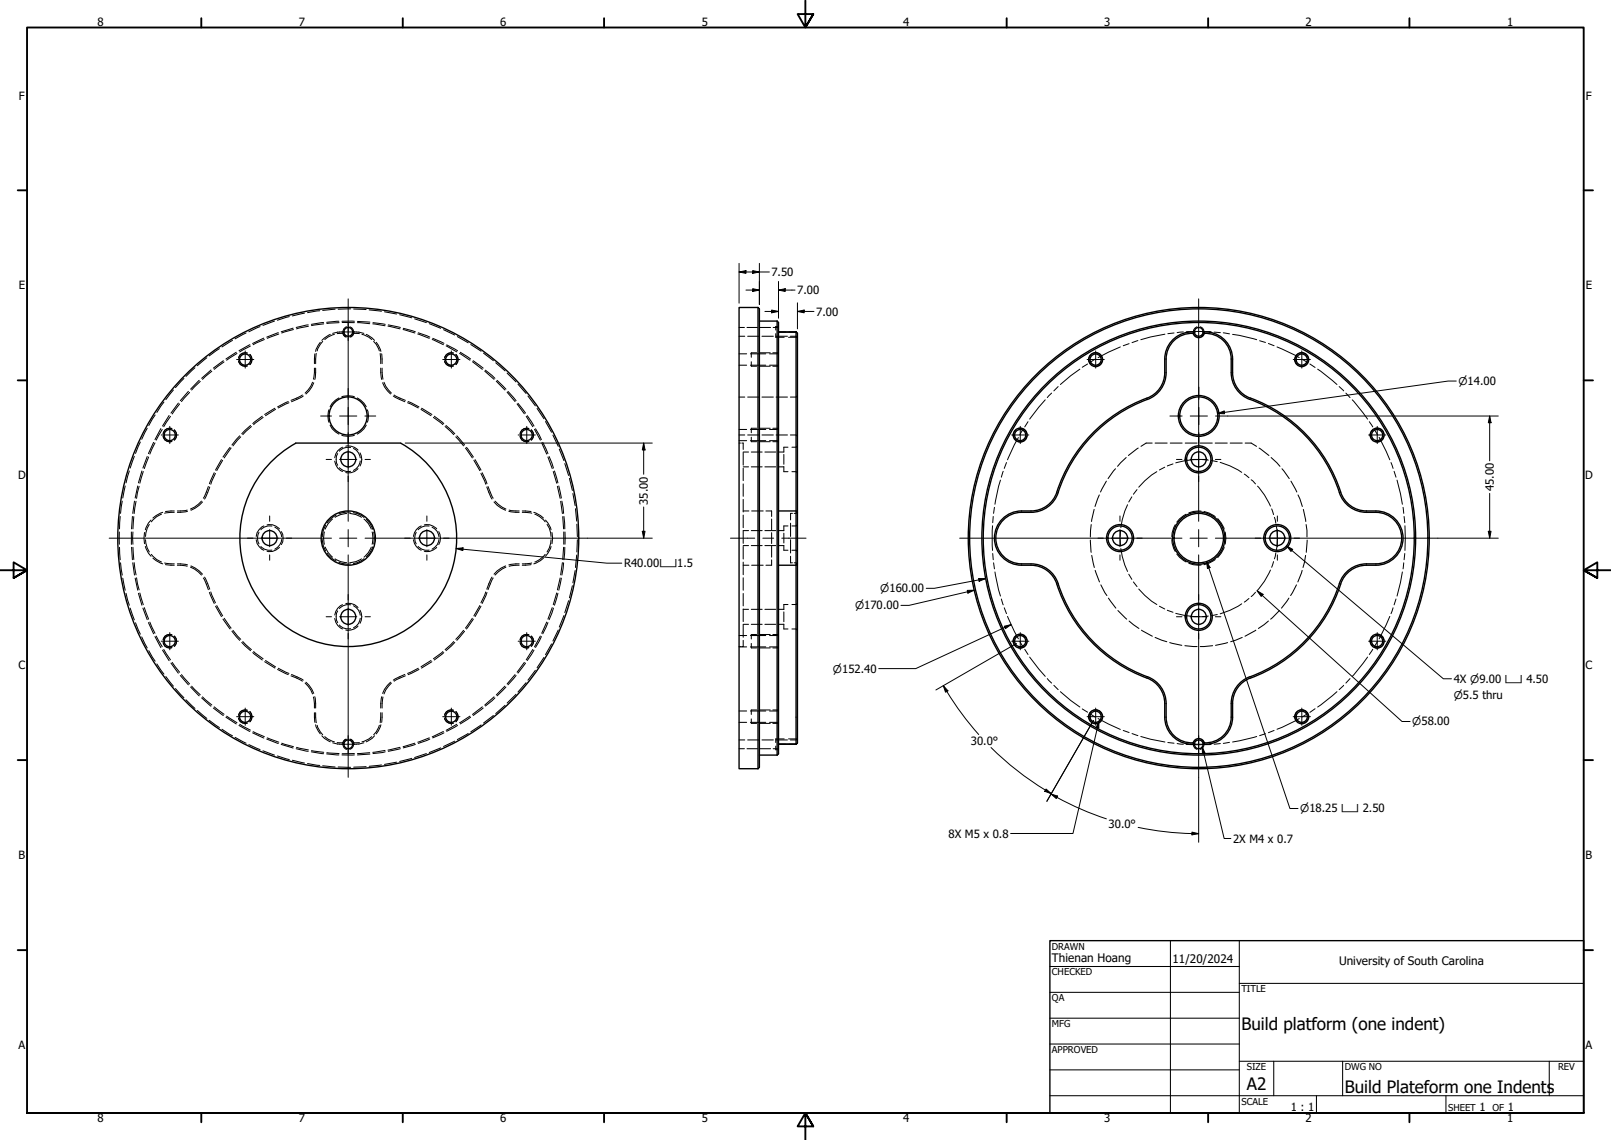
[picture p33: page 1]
4X ⌀9.00 ⌴ 4.50 ⌀5.5 thru

DRAWN Thienan Hoang | 11/20/2024 | University of South Carolina

CHECKED

TITLE
Build platform (one indent)

MFG

APPROVED

SIZE A2 | DWG NO Build Plateform one Indents | REV

SCALE 1 : 1 | | SHEET 1 OF 1

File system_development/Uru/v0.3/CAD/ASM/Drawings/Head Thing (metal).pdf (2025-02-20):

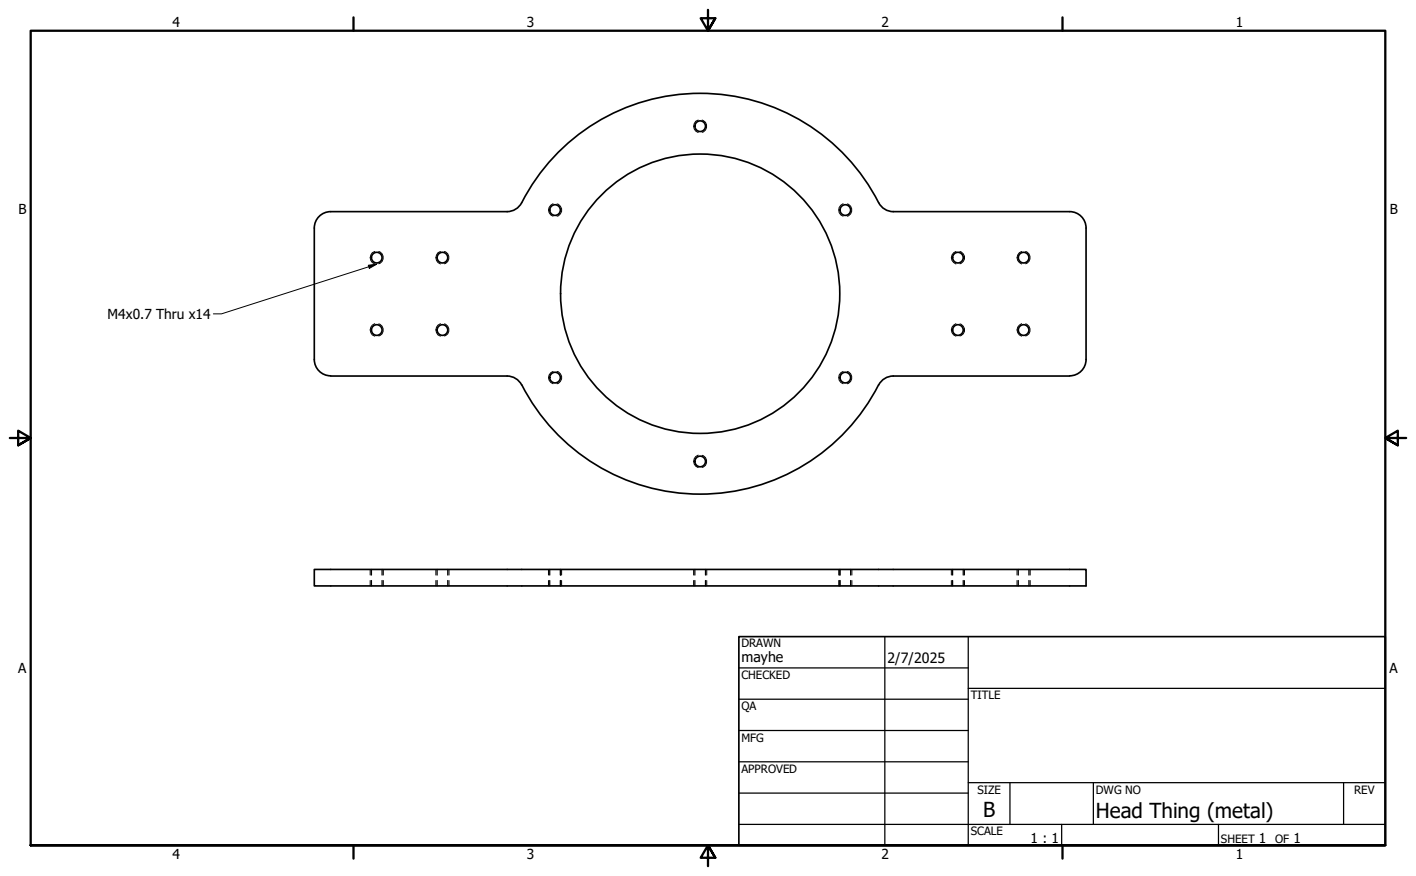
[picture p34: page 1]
M4x0.7 Thru x14

DRAWN mayhe | 2/7/2025

CHECKED

MFG

APPROVED

SIZE B | DWG NO Head Thing (metal) | REV

SCALE 1 : 1 | | SHEET 1 OF 1

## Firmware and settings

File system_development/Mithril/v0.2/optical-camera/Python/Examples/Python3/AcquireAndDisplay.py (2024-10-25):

# coding=utf-8
# =============================================================================
# Copyright (c) 2001-2023 FLIR Systems, Inc. All Rights Reserved.
#
# This software is the confidential and proprietary information of FLIR
# Integrated Imaging Solutions, Inc. ("Confidential Information"). You
# shall not disclose such Confidential Information and shall use it only in
# accordance with the terms of the license agreement you entered into
# with FLIR Integrated Imaging Solutions, Inc. (FLIR).
#
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
# This AcquireAndDisplay.py shows how to get the image data, and then display images in a GUI.
# This example relies on information provided in the ImageChannelStatistics.py example.
#
# This example demonstrates how to display images represented as numpy arrays.
# Currently, this program is limited to single camera use.
# NOTE: keyboard and matplotlib must be installed on Python interpreter prior to running this example.
#
# Please leave us feedback at: https://www.surveymonkey.com/r/TDYMVAPI
# More source code examples at: https://github.com/Teledyne-MV/Spinnaker-Examples
# Need help? Check out our forum at: https://teledynevisionsolutions.zendesk.com/hc/en-us/community/topics


import os
import PySpin
import matplotlib.pyplot as plt
import sys
import keyboard
import time

global continue_recording
continue_recording = True


def handle_close(evt):
    """
    This function will close the GUI when close event happens.

    :param evt: Event that occurs when the figure closes.
    :type evt: Event
    """

    global continue_recording
    continue_recording = False


def acquire_and_display_images(cam, nodemap, nodemap_tldevice):
    """
    This function continuously acquires images from a device and display them in a GUI.

    :param cam: Camera to acquire images from.
    :param nodemap: Device nodemap.
    :param nodemap_tldevice: Transport layer device nodemap.
    :type cam: CameraPtr
    :type nodemap: INodeMap
    :type nodemap_tldevice: INodeMap
    :return: True if successful, False otherwise.
    :rtype: bool
    """
    global continue_recording

    sNodemap = cam.GetTLStreamNodeMap()

    # Change bufferhandling mode to NewestOnly
    node_bufferhandling_mode = PySpin.CEnumerationPtr(sNodemap.GetNode('StreamBufferHandlingMode'))
    if not PySpin.IsReadable(node_bufferhandling_mode) or not PySpin.IsWritable(node_bufferhandling_mode):
        print('Unable to set stream buffer handling mode.. Aborting...')
        return False

    # Retrieve entry node from enumeration node
    node_newestonly = node_bufferhandling_mode.GetEntryByName('NewestOnly')
    if not PySpin.IsReadable(node_newestonly):
        print('Unable to set stream buffer handling mode.. Aborting...')
        return False

    # Retrieve integer value from entry node
    node_newestonly_mode = node_newestonly.GetValue()

    # Set integer value from entry node as new value of enumeration node
    node_bufferhandling_mode.SetIntValue(node_newestonly_mode)

    print('*** IMAGE ACQUISITION ***\n')
    try:
        node_acquisition_mode = PySpin.CEnumerationPtr(nodemap.GetNode('AcquisitionMode'))
        if not PySpin.IsReadable(node_acquisition_mode) or not PySpin.IsWritable(node_acquisition_mode):
            print('Unable to set acquisition mode to continuous (enum retrieval). Aborting...')
            return False

        # Retrieve entry node from enumeration node
        node_acquisition_mode_continuous = node_acquisition_mode.GetEntryByName('Continuous')
        if not PySpin.IsReadable(node_acquisition_mode_continuous):
            print('Unable to set acquisition mode to continuous (entry retrieval). Aborting...')
            return False

        # Retrieve integer value from entry node
        acquisition_mode_continuous = node_acquisition_mode_continuous.GetValue()

        # Set integer value from entry node as new value of enumeration node
        node_acquisition_mode.SetIntValue(acquisition_mode_continuous)

        print('Acquisition mode set to continuous...')

        #  Begin acquiring images
        #
        #  *** NOTES ***
        #  What happens when the camera begins acquiring images depends on the
        #  acquisition mode. Single frame captures only a single image, multi
        #  frame catures a set number of images, and continuous captures a
        #  continuous stream of images.
        #
        #  *** LATER ***
        #  Image acquisition must be ended when no more images are needed.
        cam.BeginAcquisition()

        print('Acquiring images...')

        #  Retrieve device serial number for filename
        #
        #  *** NOTES ***
        #  The device serial number is retrieved in order to keep cameras from
        #  overwriting one another. Grabbing image IDs could also accomplish
        #  this.
        device_serial_number = ''
        node_device_serial_number = PySpin.CStringPtr(nodemap_tldevice.GetNode('DeviceSerialNumber'))
        if PySpin.IsReadable(node_device_serial_number):
            device_serial_number = node_device_serial_number.GetValue()
            print('Device serial number retrieved as %s...' % device_serial_number)

        # Close program
        print('Press enter to close the program..')

        # Figure(1) is default so you can omit this line. Figure(0) will create a new window every time program hits this line
        fig = plt.figure(1)

        # Close the GUI when close event happens
        fig.canvas.mpl_connect('close_event', handle_close)

        # Retrieve and display images
        while(continue_recording):
            try:

                #  Retrieve next received image
                #
                #  *** NOTES ***
                #  Capturing an image houses images on the camera buffer. Trying
                #  to capture an image that does not exist will hang the camera.
                #
                #  *** LATER ***
                #  Once an image from the buffer is saved and/or no longer
                #  needed, the image must be released in order to keep the
                #  buffer from filling up.
                
                image_result = cam.GetNextImage(1000)

                #  Ensure image completion
                if image_result.IsIncomplete():
                    print('Image incomplete with image status %d ...' % image_result.GetImageStatus())

                else:                    

                    # Getting the image data as a numpy array
                    image_data = image_result.GetNDArray()

                    # Draws an image on the current figure
                    plt.imshow(image_data, cmap='gray')

                    # Interval in plt.pause(interval) determines how fast the images are displayed in a GUI
                    # Interval is in seconds.
                    plt.pause(0.001)

                    # Clear current reference of a figure. This will improve display speed significantly
                    plt.clf()
                    
                    # If user presses enter, close the program
                    if keyboard.is_pressed('ENTER'):
                        print('Program is closing...')
                        
                        # Close figure
                        plt.close('all')             
                        input('Done! Press Enter to exit...')
                        continue_recording=False                        

                #  Release image
                #
                #  *** NOTES ***
                #  Images retrieved directly from the camera (i.e. non-converted
                #  images) need to be released in order to keep from filling the
                #  buffer.
                image_result.Release()

            except PySpin.SpinnakerException as ex:
                print('Error: %s' % ex)
                return False

        #  End acquisition
        #
        #  *** NOTES ***
        #  Ending acquisition appropriately helps ensure that devices clean up
        #  properly and do not need to be power-cycled to maintain integrity.
        cam.EndAcquisition()

    except PySpin.SpinnakerException as ex:
        print('Error: %s' % ex)
        return False

    return True


def run_single_camera(cam):
    """
    This function acts as the body of the example; please see NodeMapInfo example
    for more in-depth comments on setting up cameras.

    :param cam: Camera to run on.
    :type cam: CameraPtr
    :return: True if successful, False otherwise.
    :rtype: bool
    """
    try:
        result = True

        nodemap_tldevice = cam.GetTLDeviceNodeMap()

        # Initialize camera
        cam.Init()

        # Retrieve GenICam nodemap
        nodemap = cam.GetNodeMap()

        # Acquire images
        result &= acquire_and_display_images(cam, nodemap, nodemap_tldevice)

        # Deinitialize camera
        cam.DeInit()

    except PySpin.SpinnakerException as ex:
        print('Error: %s' % ex)
        result = False

    return result


def main():
    """
    Example entry point; notice the volume of data that the logging event handler
    prints out on debug despite the fact that very little really happens in this
    example. Because of this, it may be better to have the logger set to lower
    level in order to provide a more concise, focused log.

    :return: True if successful, False otherwise.
    :rtype: bool
    """
    result = True

    # Retrieve singleton reference to system object
    system = PySpin.System.GetInstance()

    # Get current library version
    version = system.GetLibraryVersion()
    print('Library version: %d.%d.%d.%d' % (version.major, version.minor, version.type, version.build))

    # Retrieve list of cameras from the system
    cam_list = system.GetCameras()

    num_cameras = cam_list.GetSize()

    print('Number of cameras detected: %d' % num_cameras)

    # Finish if there are no cameras
    if num_cameras == 0:

        # Clear camera list before releasing system
        cam_list.Clear()

        # Release system instance
        system.ReleaseInstance()

        print('Not enough cameras!')
        input('Done! Press Enter to exit...')
        return False

    # Run example on each camera
    for i, cam in enumerate(cam_list):

        print('Running example for camera %d...' % i)

        result &= run_single_camera(cam)
        print('Camera %d example complete... \n' % i)

    # Release reference to camera
    # NOTE: Unlike the C++ examples, we cannot rely on pointer objects being automatically
    # cleaned up when going out of scope.
    # The usage of del is preferred to assigning the variable to None.
    del cam

    # Clear camera list before releasing system
    cam_list.Clear()

    # Release system instance
    system.ReleaseInstance()

    input('Done! Press Enter to exit...')
    return result


if __name__ == '__main__':
    if main():
        sys.exit(0)
    else:
        sys.exit(1)

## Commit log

2024-05-07 add camera hardware design
    [Close Camera Holder.ipt, Close Camera Holder.stl, flir_holder.f3d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]
2024-05-13 Create Cylinder Spacer Top_Q.ipt
    Cylinder Spacer Top Quadrant 1
    [Cylinder Spacer Top_Q.ipt]
2024-05-16 Added File Directory
    New folders were added to sort part models into sections
    [Cylinder Spacer Top_Q.ipt]
2024-05-16 Added CAD files
    Added CAD files and sorted based on category
    [14159_m.ipt, 20-2020-160-CL.ipt, 20-2020-200-CL.ipt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]
2024-05-17 Fixed Assembly not working
    Main assembly should now work without missing parts. Created an ipj file so we can work directly off of the local github.
    [11-4310.0001.ipt, 11-4310.ipt, 14159_m.0001.ipt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]
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2024-05-19 named variations after mythical materials.
    [11-4310.0001.ipt, 11-4310.ipt, 14159_m.0001.ipt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]
2024-05-19 Fixed Workgroup search paths on inventor
    [Custom Cover Full Assembly.0030.iam, Custom Cover Full Assembly.0032.iam, Custom Cover Full Assembly.iam]
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2024-05-21 Reorganized Orichalicum Hardware Folder
    Cylinder-parts now includes all cover assembly pieces, pieces cut for printing bed, and STLs.
    [14159_m.0001.ipt, 14159_m.ipt, 20-2020-160-CL.0001.ipt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]
2024-05-21 Deleted Extra v0.1 file
    [11-4310.0001.ipt, 11-4310.ipt, 14159_m.0001.ipt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]
2024-05-22 Cylinder Segment.ipt
    cylinder-segments folder updated with all parts.
    [Cylinder Segment .ipt]
2024-05-22 Update with Galvo Software Folder
    [91292A110_18-8 Stainless Steel Socket Head Screw.ipt, GHS003_M-Step.ipt, GVS102-Step.ipt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]
2024-05-24 Laser Pointer System
    Includes a simple model of the laser pen and a housing (top and bottom) to take the place of "Updated Laser Scanner" for prototyping.
    [Laser_Pen_Housing_Bottom.ipt, Laser_Pen_Housing_Top.ipt, Laser_Pointer_Model.ipt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]
2024-05-26 STLs of all prints for printing
    3 files in "laser-vibrometer" folder, 15 items in "stl-files-full pieces" (found in cylinder-parts folder)
    [Cylinder Segment - 01.stl, Cylinder Segment - 02.stl, Cylinder Segment - 03.stl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]
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2024-05-27 Fixed main cover assembly
    [11-4310.ipt, 25-4136.ipt, ANSI B18.3.1M - M2x0.4 x 20(1).ipt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]
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2024-06-05 Added files related to the printer and custom cover
    [Cover.ipt, Head Thing.ipt, Laser w_ silver v4.iam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]
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2024-06-07 Made V0.2 file and made changes to many files
    [11-4310.ipt, 14159_m.0001.ipt, 14159_m.ipt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]
2024-06-10 Made new parts for the cover
    [11-4310.ipt, 13022_m.ipt, 14159_m.0001.ipt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]
2024-06-12 added galvo housing and overhauled the full printer assembly
    [Custom Cover Full Assembly v0.2.0043.iam, Custom Cover Full Assembly v0.2.0048.iam, Custom Cover Full Assembly v0.2.iam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]
2024-06-12 Deleted files that had long names
    [Cylinder Segment - 01.0003.ipt, Cylinder Segment - 01.0013.ipt, Cylinder Segment - 01.ipt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]
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2024-06-18 Cover Prototype Frame
    new 80/20 parts
    updated assemblies
    PZT folder & models created
    [20-2020-104.025.ipt, 20-2020-104.525.0004.ipt, 20-2020-105.ipt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]
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2024-06-28 Changes to printer
    Magnet Failsafe
    [Cylinder 80-20 Spacer_1.stl, Cylinder 80-20 Spacer_2.stl, Cylinder Base Bottom.ipt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]
2024-07-02 Custom cover Step file uploaded
    [1078N29_Class 10.9 High-Strength Steel Thread.0001.ipt, 1078N29_Class 10.9 High-Strength Steel Thread.ipt, Adapter Plate.0001.ipt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]
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2024-07-17 Changed gavlo placement and tweaked housing
    [13084_m.ipt, 14056_m.0001.ipt, 14056_m.ipt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]
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2024-09-25 REplacement rings and newly proposed PZT setup
    [90133A240_Oil-Resistant Neoprene Rubber Seali.ipt, 91290.ipt, 91294A208_Black-Oxide Alloy Steel Hex Drive F.ipt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]
2024-10-11 updated some rings to fit
    [Adapter Plate.0001.ipt, Adapter Plate.0002.ipt, Adapter Plate.ipt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]
2024-10-23 CAD model of FLIR Blackfly
    [flircamera+lens.ipt]
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2024-10-25 Adjustments to PZT system
    [Adapter Plate.0002.ipt, Adapter Plate.0004.ipt, Adapter Plate.ipt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]
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2024-11-02 New 240 mm glass design
    [130 mm Glass.ipt, 260 mm Glass.ipt, 260mm Housing 1.0008.ipt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]
2024-11-11 Design for one glass setup and modified built platform
    [240mm Housing 1.stl, 240mm housing 2.stl, 260 mm Glass.0001.ipt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]
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2024-11-18 UPdated indents in build plateform
    [Build Plateform Indents.0017.ipt, Build Plateform Indents.0020.ipt, Build Plateform Indents.ipt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]
2024-12-06 Metal + Plastic version of build platform
    [1078N152_Class 10.9 High-Strength Steel Threa.ipt, 90133A240_Oil-Resistant Neoprene Rubber Seali.ipt, 91290.ipt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]
2024-12-09 Git hub clean up
    [Build Plateform one Indents (metal).stp, Build Plateform one Indents.0004.dwg, Build Plateform one Indents.0006.dwg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]
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2025-02-01 added new folders and pictures of the duck
    [Close Camera Holder.ipt, Close Camera Holder.stl, Cover.0001.ipt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]
2025-02-04 Replaced Ducky with Optical Camera Only Cad Pic
    [260 mm Glass.ipt, 300mm Housing 1.3mf, 300mm Housing 1.ipt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]
2025-02-07 Updated Some Build platforms and Cover camera only
    [Build Plateform one Indents (metal).0014.ipt, Build Plateform one Indents (metal).0015.ipt, Build Plateform one Indents (metal).ipt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]
2025-02-07 Modified Optical Camera Only Setup
    [Build Plateform one Indents (metal).0015.ipt, Build Plateform one Indents (metal).0016.ipt, Build Plateform one Indents (metal).ipt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]
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2025-02-20 More changes to optical camera only setup
    [Camera Bracket.3mf, Camera Bracket.stp, Cover Optical Camera Only.0021.iam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]
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2025-03-04 Update cover
    Deleted grove and adjusted handle holes.
    [Cover (Optical Camera).0025.ipt, Cover (Optical Camera).ipt, Updated Cover With Grove.ipt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]
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2025-03-20 Fixed labview code for thermal camera
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2025-05-01 updated replacement rings
    [C .Replace - 01.0001.ipt, C .Replace - 01.ipt, C .Replace - 02.0001.ipt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]
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2025-05-08 Optical and Event Camera Holders
    Ability to have both the optical and event cameras.
    [CoverHolder_Both.0001.ipt, CoverHolder_Both.ipt, Cylinder Segment Both Cameras v01.0010.ipt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]
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2025-06-17 Event Cam install guide
    Added a text file that walks you through how to install the files required to control the camera
    [090869.ipt, 090870.ipt, 090879-XX_090879-04.ipt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]
